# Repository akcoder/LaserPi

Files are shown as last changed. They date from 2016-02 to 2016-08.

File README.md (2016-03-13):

# LaserPi
LaserPi is a Raspberry Pi 2 based auxiliary controller for your laser cutter. Why would you want an auxiliary controller?

LaserPi reads sensor data (temperature, and coolant flow currently) and displays this data on the screen. You can set alarm
information based on the values from the sensors. You can be notified if the temperature goes above a user-defined value, or
if the coolant flow rate goes below a user-defined value. You can also turn on/off your chiller, exhaust, air assist pump,
and lights.

LaserPi can also act upon inputs from your laser controller. Most laser controllers have 4-5 GPIO pins that are set when
the controller is doing certain operations. For example, on the Leetro MPC-6515, output pin 4 is pulled low when the controller
is working. And output pin 1 is pulled low when the air assist box is checked for the layer.

So what can be done with these outputs? LaserPi will automatically turn on your exhaust fan when the laser controller starts
a job, and will keep the exhaust fan running for a user definable period of time after the job is finished to clear away all
the fumes. Have you ever left the air assist box checked by accident and had your air pump turn on when you didn't want it to?
I have, many times and I have to pause my machine and unplug the air assist.

## How does it work?
The brains of the operation is a Raspberry Pi with the code being Python using the QT GUI framework. Data is acquired
from the sensors, and GPIO pins on the Pi, and decisions are made.

###Sensors
*  [Waterproof 1-wire temperature sensors](http://www.aliexpress.com/wholesale?SearchText=waterproof+DS18b20)
*  [YF-S201 fluid flow sensor](http://www.dx.com/p/yf-s201-hall-effect-water-flow-counter-sensor-black-217625)

###Glue components
*  [Logic Level Converter - Bi-Directional](https://www.sparkfun.com/products/12009)
*  [Fotek SSR-25 DA Relays](http://www.amazon.com/dp/B004HZN628)

Here is a work in progress screen shot of LaserPi
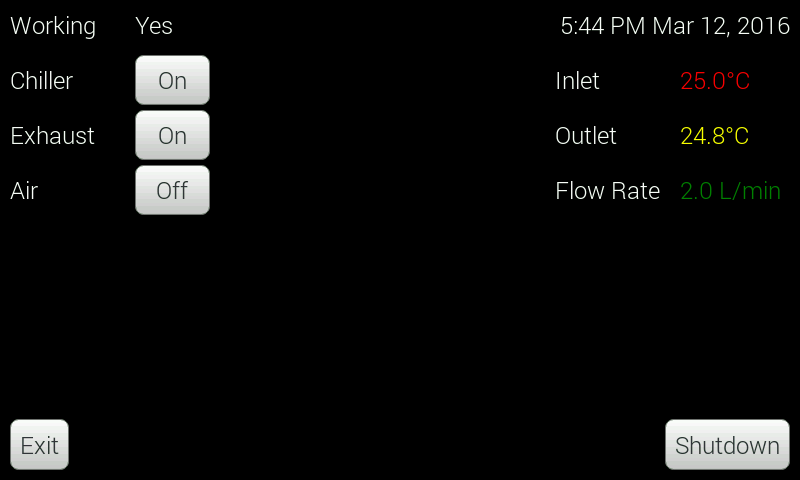
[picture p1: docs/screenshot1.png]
Work in progress


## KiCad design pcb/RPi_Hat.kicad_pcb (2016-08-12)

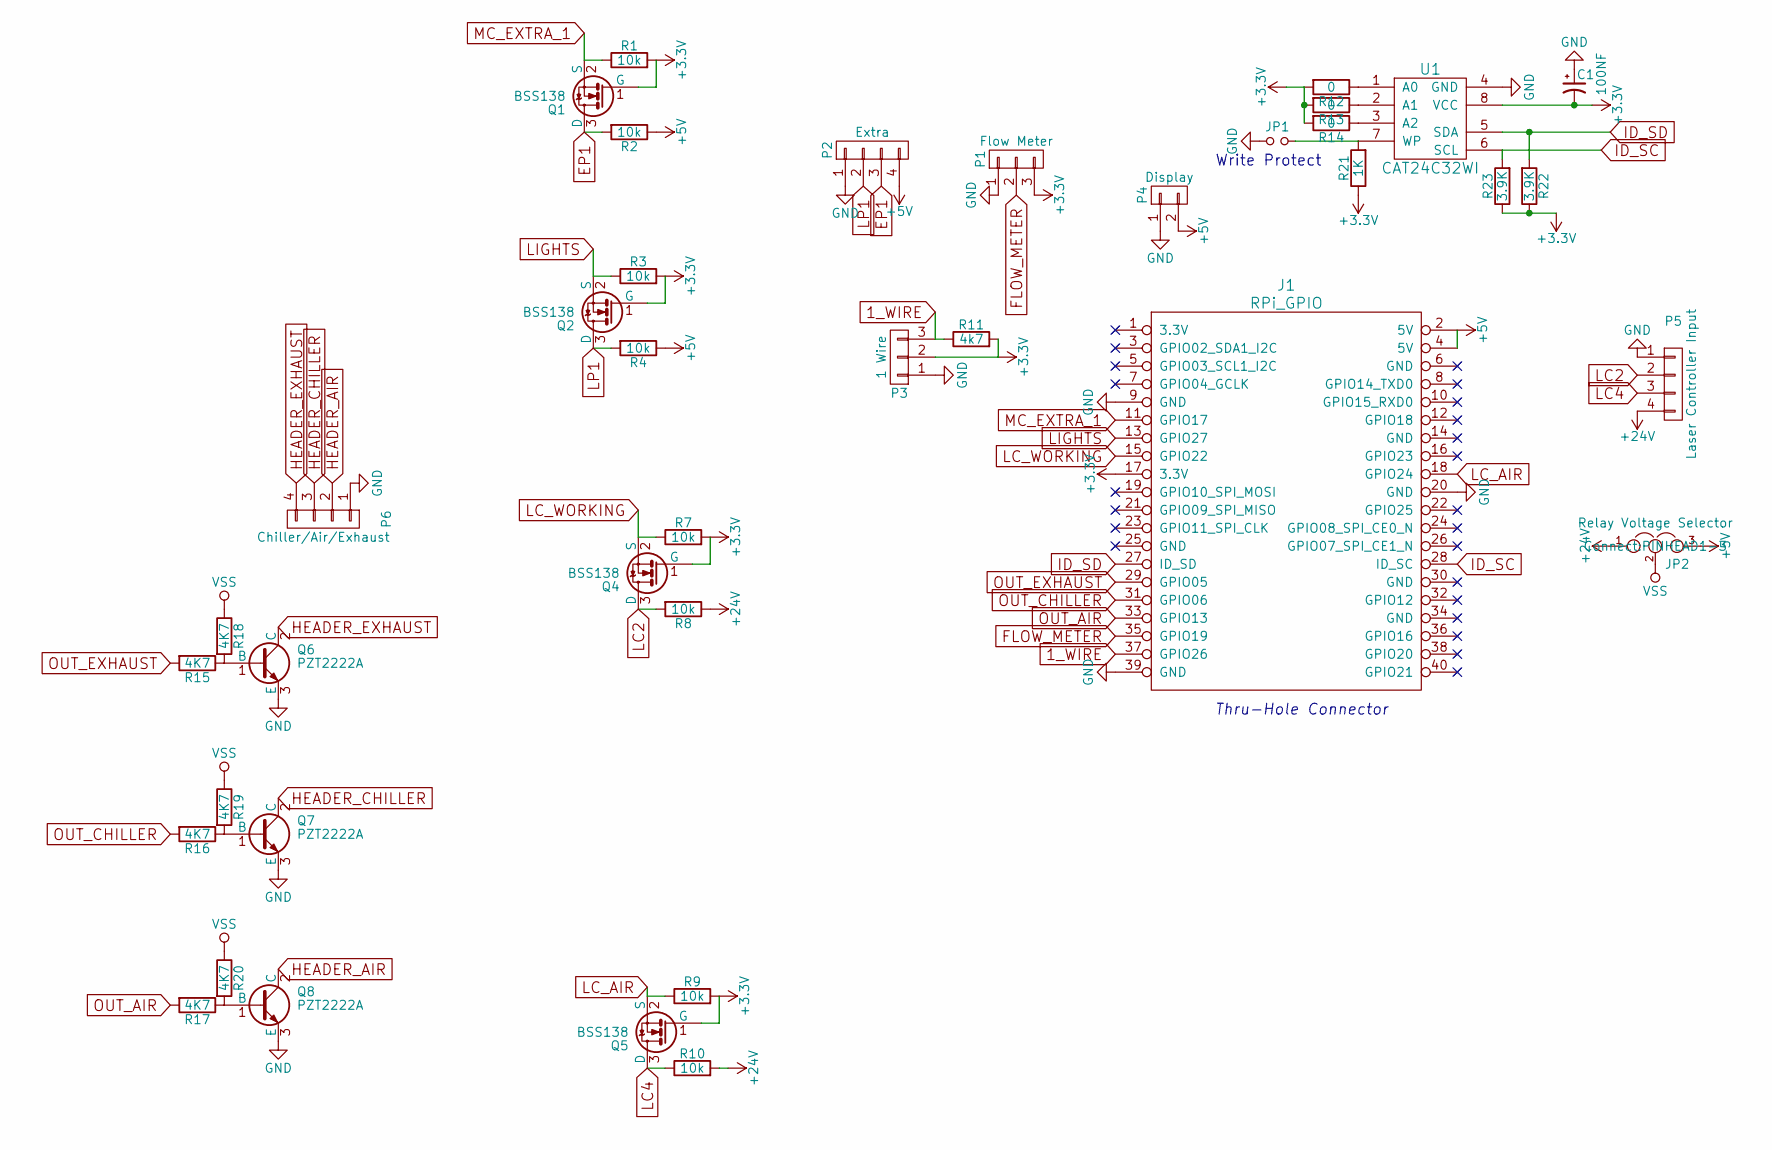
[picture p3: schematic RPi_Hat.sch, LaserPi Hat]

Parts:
C1: 100NF; C_1206_HandSoldering
J1: RPi_GPIO; Pin_Header_Straight_2x20
JP1: Jumper_NO_Small; PINHEAD1-2
JP2: Relay Voltage Selector; PINHEAD1-3
P1: Flow Meter; TerminalBlock_Pheonix_MPT-2.54mm_3pol
P2: Extra; TerminalBlock_Pheonix_MPT-2.54mm_4pol
P3: 1 Wire; TerminalBlock_Pheonix_MPT-2.54mm_3pol
P4: Display; TerminalBlock_Pheonix_MPT-2.54mm_2pol
P5: Laser Controller Input; TerminalBlock_Pheonix_MPT-2.54mm_4pol
P6: Chiller/Air/Exhaust; TerminalBlock_Pheonix_MPT-2.54mm_4pol
Q1, Q2, Q4, Q5: BSS138; SOT-23
Q6, Q7, Q8: PZT2222A; SOT-23
R1, R2, R3, R4, R7, R8, R9, R10: 10k; R_1206_HandSoldering
R11: 4k7; R_1206_HandSoldering
R12, R13, R14: 0; R_0402
R15, R16, R17, R18, R19, R20: 4K7; R_1206_HandSoldering
R21: 1K; R_1206_HandSoldering
R22, R23: 3.9K; R_1206_HandSoldering
U1: CAT24C32WI; SOIC-8-N

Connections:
1_WIRE: J1.37 (GPIO26), P3.3, R11.1
+3V3: C1.2, J1.17 (3.3V), P1.3, P3.2, Q1.1 (G), Q2.1 (G), Q4.1 (G), Q5.1 (G), R1.2, R3.2, R7.2, R9.2, R11.2, R12.2, R13.2, R14.2, R21.1, R22.1, R23.1, U1.8 (VCC)
+5V: J1.2 (5V), J1.4 (5V), JP2.3, P2.4, P4.2, R2.1, R4.1
+24V: JP2.1, P5.4, R8.1, R10.2
EP1: P2.3, Q1.3 (D), R2.2
FLOW_METER: J1.35 (GPIO19), P1.2
GND: C1.1, J1.9 (GND), J1.20 (GND), J1.39 (GND), JP1.1, P1.1, P2.1, P3.1, P4.1, P5.1, P6.1, Q6.3 (E), Q7.3 (E), Q8.3 (E), U1.4 (GND)
HEADER_AIR: P6.2, Q8.2 (C)
HEADER_CHILLER: P6.3, Q7.2 (C)
HEADER_EXHAUST: P6.4, Q6.2 (C)
ID_SC: J1.28 (ID_SC), R23.2, U1.6 (SCL)
ID_SD: J1.27 (ID_SD), R22.2, U1.5 (SDA)
LC2: P5.2, Q4.3 (D), R8.2
LC4: P5.3, Q5.3 (D), R10.1
LC_AIR: J1.18 (GPIO24), Q5.2 (S), R9.1
LC_WORKING: J1.15 (GPIO22), Q4.2 (S), R7.1
LIGHTS: J1.13 (GPIO27), Q2.2 (S), R3.1
LP1: P2.2, Q2.3 (D), R4.2
MC_EXTRA_1: J1.11 (GPIO17), Q1.2 (S), R1.1
unnamed: JP1.2, R21.2, U1.7 (WP)
unnamed: Q6.1 (B), R15.1, R18.2
unnamed: Q7.1 (B), R16.1, R19.2
unnamed: Q8.1 (B), R17.1, R20.2
unnamed: R12.1, U1.1 (A0)
unnamed: R13.1, U1.2 (A1)
unnamed: R14.1, U1.3 (A2)
OUT_AIR: J1.33 (GPIO13), R17.2
OUT_CHILLER: J1.31 (GPIO06), R16.2
OUT_EXHAUST: J1.29 (GPIO05), R15.2
VSS: JP2.2, R18.1, R19.1, R20.1

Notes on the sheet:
Thru-Hole Connector
Write Protect

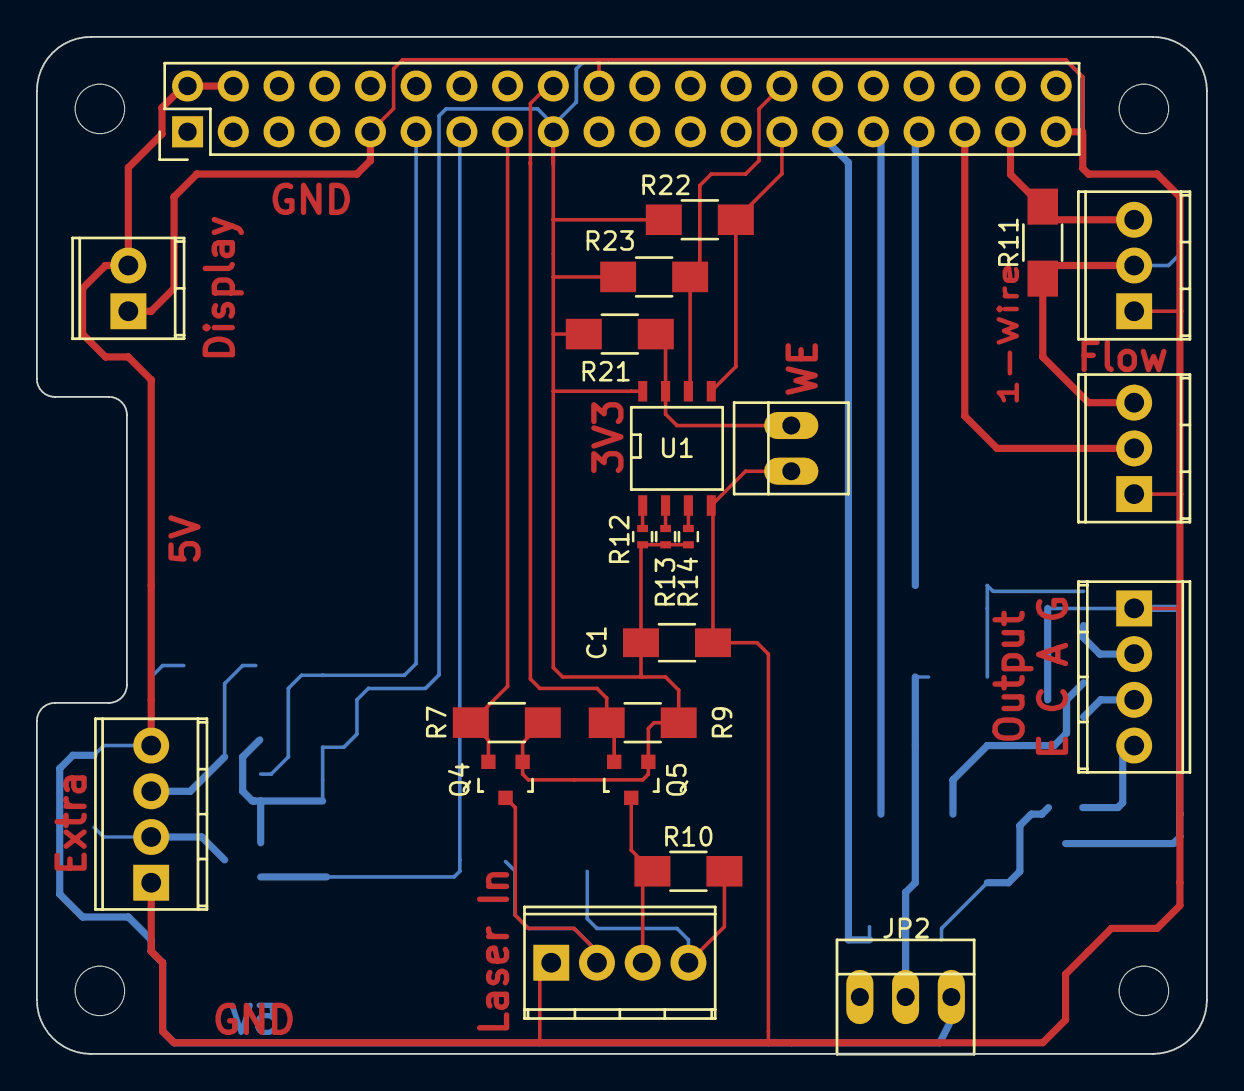
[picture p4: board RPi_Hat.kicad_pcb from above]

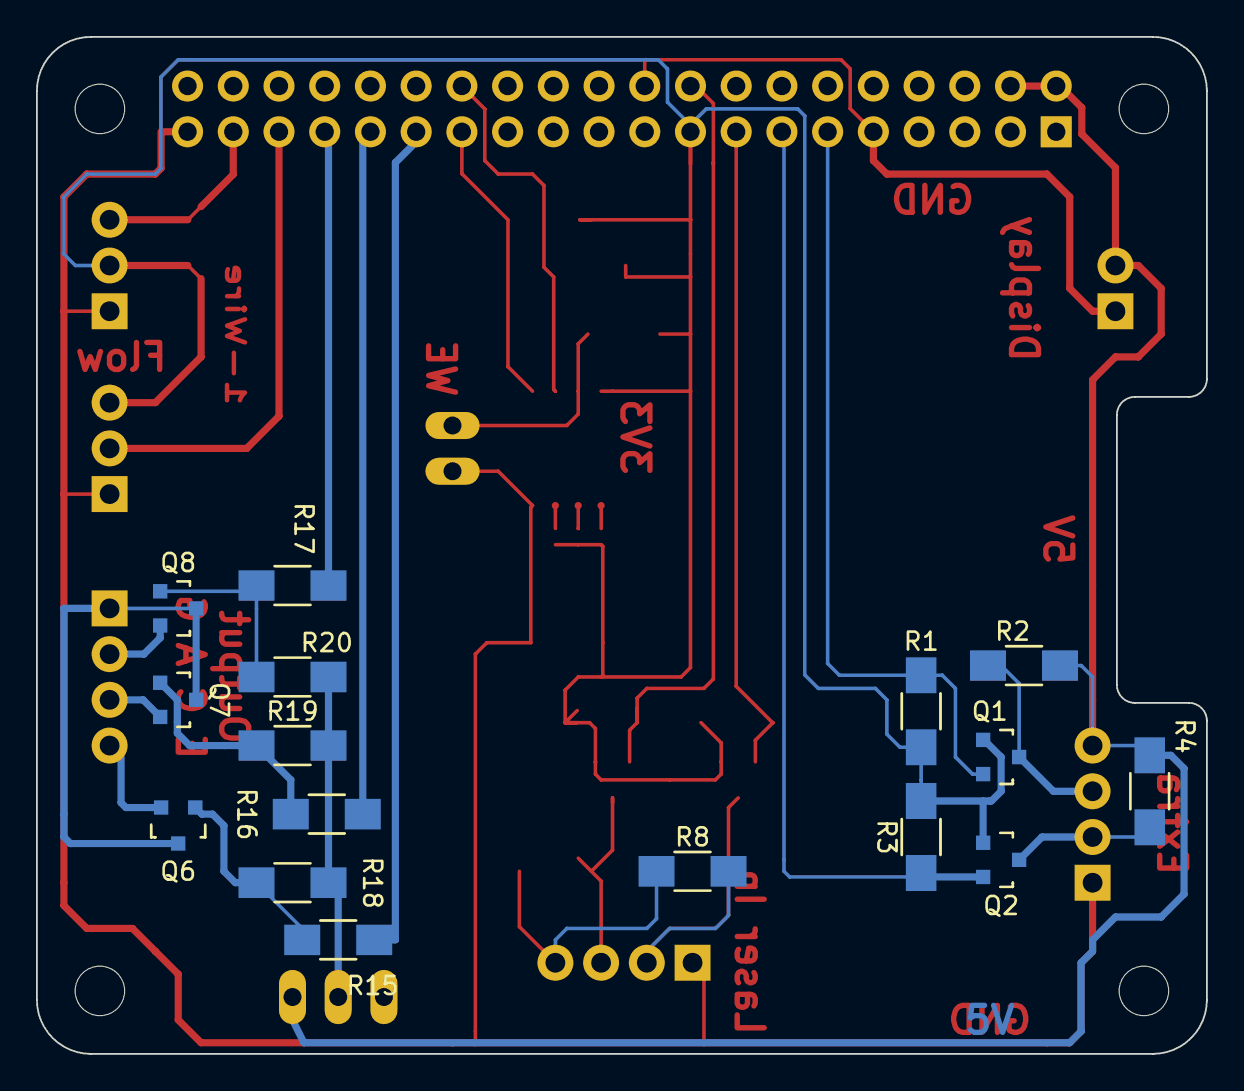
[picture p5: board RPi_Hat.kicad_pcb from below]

Board: 2 copper layers, 65.0 x 56.5 mm, 39 parts (16 on the bottom side), 30 nets.

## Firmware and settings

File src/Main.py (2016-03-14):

"""Main"""
import logging
import sys
import signal
#import ptvsd
#ptvsd.enable_attach('laserpi')

from PySide.QtGui import QApplication

from ViewModel import MainViewModel
from Views import MainView
from Controller import Controller
from Helpers.Settings import Settings

def setup_logging():
    logger = logging.getLogger('')
    logger.setLevel(logging.DEBUG)
    ch = logging.StreamHandler()
    ch.setLevel(logging.DEBUG)
    # create formatter and add it to the handlers
    formatter = logging.Formatter('%(asctime)s - %(name)s - %(levelname)s - %(message)s')
    ch.setFormatter(formatter)
    logger.addHandler(ch)

def main():
    """Main"""
    signal.signal(signal.SIGINT, signal.SIG_DFL)

    setup_logging()

    # Create Qt application and the QDeclarative view
    app = QApplication(sys.argv)

    view_model = MainViewModel()
    controller = Controller(view_model)

    main_view = MainView(view_model)

    if sys.platform == 'win32':
        main_view.show()
    else:
        main_view.showFullScreen()

    sys.exit(app.exec_())

if __name__ == "__main__":
    main()

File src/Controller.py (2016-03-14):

"""The glue between the view and viewModel"""

import os
import logging
import sys
import threading
from threading import Thread, Timer
from PySide import QtCore
from ViewModel import MainViewModel
from Helpers import Settings
from enum import IntEnum
from Helpers.PerpetualTimer import PerpetualTimer
from Helpers.Observer import Observer
from Sensors.SensorFactory import SensorFactory

if sys.platform == 'linux':
    import RPi.GPIO as GPIO

class Controller(Observer):
    """The glue between the view and viewModel"""

    __logger = logging.getLogger(__name__)
    def __init__(self, viewModel: MainViewModel):
        Observer.__init__(self)
        self.__view_model = viewModel
        self.__gpio_is_setup = False
        self.__exhaust_timer = None
        self.__view_model.onChillerChanged.connect(self.chiller_changed)
        self.__view_model.onAirChanged.connect(self.air_changed)
        self.__view_model.onExhaustChanged.connect(self.exhaust_changed)
        self.__view_model.onExitClicked.connect(self.close)
        self.__view_model.onShutdownClicked.connect(self.shutdown)
        self.__sensors = []

        if sys.platform == 'linux':
            self._states = {
                Settings.instance.pins.input.working:GPIO.LOW,
                Settings.instance.pins.input.airTrigger:GPIO.LOW
            }

            self.__gpio_thread = Thread(target=self.__setup_gpio)
            self.__gpio_thread.setDaemon(1)
            self.__gpio_thread.start()

        self.observe('temp_changed', self.handle_temp_changed)
        self.observe('flow_changed', self.handle_flow_changed)

        for key in Settings.instance.sensors._fields:
            config = getattr(Settings.instance.sensors, key)
            sensor = SensorFactory.factory(key, config)
            sensor.start();
            self.__sensors.append(sensor)

    def __del__(self):
        self.__logger.info('Destructor called, cleaning up')
        self.cleanup()

    def __setup_gpio(self) -> None:
        self.__logger.info("Setting up GPIO")
        GPIO.setmode(GPIO.BCM)

        for key in Settings.instance.pins.output._fields:
            pin = getattr(Settings.instance.pins.output, key)
            self.__logger.debug("Setting GPIO {0} for output".format(pin))
            GPIO.setup(pin, GPIO.OUT)

        GPIO.setup(Settings.instance.pins.input.working, GPIO.IN, pull_up_down=GPIO.PUD_DOWN)
        GPIO.add_event_detect(Settings.instance.pins.input.working, GPIO.BOTH, callback=self.working_changed, bouncetime=25)

        GPIO.setup(Settings.instance.pins.input.airTrigger, GPIO.IN, pull_up_down=GPIO.PUD_DOWN)
        GPIO.add_event_detect(Settings.instance.pins.input.airTrigger, GPIO.BOTH, callback=self.air_trigger_changed, bouncetime=25)

        self.__gpio_is_setup = True

    def close(self):
        self.__logger.info("Close called")
        self.cleanup()
        self.__logger.info("After cleanup")
        QtCore.QCoreApplication.instance().quit()

        self.__logger.info("OS exit")
        os._exit(0)
        raise SystemExit

    @classmethod
    def shutdown(cls):
        if sys.platform == "linux":
            try:
                command = "/usr/bin/sudo /sbin/shutdown --halt now"
                import subprocess
                process = subprocess.Popen(command.split(), stdout=subprocess.PIPE)
                output = process.communicate()[0]
                self.__logger.info(output)
            except Exception as ex:
                self.__logger.error(ex)
                self.__logger.error("Unable to shutdown")
                sys.exit()
        else:
            sys.exit()

    def cleanup(self):
        self.__logger.info("Cleanup called")

        for sensor in self.__sensors:
            sensor.stop()

        if sys.platform == 'linux' and self.__gpio_is_setup:
            self.__logger.info("Cleaning up GPIO")
            GPIO.cleanup()

    def handle_temp_changed(self, name: str, value: float) -> None:
        self.__view_model.onTemperatureChanged.emit(name, value)

    def handle_flow_changed(self, name: str, value: float) -> None:
        self.__view_model.onFlowRateChanged.emit(name, value)

    def air_changed(self) -> None:
        if sys.platform != 'linux':
            return

        self.set_air_state(GPIO.HIGH if self.__view_model.air else GPIO.LOW)

    @QtCore.Slot()
    def air_trigger_changed(self, channel=None):
        if  GPIO.input(channel) == GPIO.HIGH:
            if  self._states[channel] == GPIO.LOW:
                self.__logger.debug("Turning air on because triggered")
                self.__view_model.air = True

            self._states[channel] = GPIO.HIGH
        elif self._states[channel] == GPIO.HIGH and self.__view_model.air:
            self.__logger.debug("Turning air off because triggered")
            self.__view_model.air = False
            self._states[channel] = GPIO.LOW

    def set_air_state(self, state):
        self.set_pin_state(Settings.instance.pins.output.airOutput, state)

    def set_pin_state(self, pin: int, state: bool) -> None:
        self.__logger.debug("Setting GPIO {0} to {1}".format(pin, "HIGH" if state else "LOW"))
        GPIO.output(pin, GPIO.HIGH if state else GPIO.LOW)

    def working_changed(self, channel):
        if  GPIO.input(channel) == GPIO.HIGH:
            if  self._states[channel] == GPIO.LOW:
                self.__logger.info("Laser is working")
                self.__view_model.working = True
                self.turn_exhaust_on()

                if self.__exhaust_timer is not None:
                    self.__exhaust_timer.cancel()
                    self.__exhaust_timer = None

            self._states[channel] = GPIO.HIGH
        elif self._states[channel] == GPIO.HIGH:
            if self.__view_model.exhaust:
                assert self.__exhaust_timer is None, "Exhaust timer should have been set to null!"

                seconds = Settings.instance.exhaust_time_after_finished
                self.__logger.info("Setting exhaust off timer for %d seconds" % seconds)
                self.__exhaust_timer = Timer(seconds, self.turn_exhaust_off)
                self.__exhaust_timer.start()
                self.__view_model.working = False
            self._states[channel] = GPIO.LOW

    def turn_exhaust_on(self):
        self.__logger.debug("Turning exhaust fan on")
        self.__view_model.exhaust = True
        self.set_pin_state(Settings.instance.pins.output.exhaust, GPIO.HIGH)

    def turn_exhaust_off(self):
        self.__logger.debug("Turning exhaust fan off")
        self.__view_model.exhaust = False
        self.__exhaust_timer = None
        self.set_pin_state(Settings.instance.pins.output.exhaust, GPIO.LOW)

    @QtCore.Slot()
    def chiller_changed(self):
        if sys.platform == 'linux':
            self.set_pin_state(Settings.instance.pins.output.chiller, self.__view_model.chiller)
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

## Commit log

2016-02-29 - Add exit button - Make exiting the app cleanup the GPIO - Misc pylint cleanups - Trigger more GPIOs - Figure out the final pin configuration
2016-03-05 Add Temperature and FlowMeter support Add settings support
2016-03-06 Rename LaserPi -> LaserPiPy
2016-03-06 LaserPiIot initial commit
2016-03-06 Add the LaserPiPy project files
2016-03-10 Dynamically load the temperature sensors from the config and add them to the display Do a fade in animation when the temp is first set in the view
2016-03-11 Setup flow rate sensor
    Setup the flow rate sensor
    Don't use a property on the view model to hold the degree symbol, put it
    in the Temperature.js file
2016-03-11 Show units for temperature
    Don't do all the rejiggering of the config json to and from an object to
    put it into the QML.
2016-03-12 Fix layout issues, temp changes
    Fix some layout nits
    Put the degree symbol and temp units in their own label and right align
    the temperature
    [Temperature.py]
2016-03-12 Use factory to create sensors
    Use the factory pattern to create the sensors, and pass the config into
    the sensors.
2016-03-12 Globals are bad!
    Get rid of all the globals in Temperature.js by using lambdas!
2016-03-12 Cleanup temperature view
    Make the temperature view more generic
    Remove the model from the temperature view and set properties on the
    view
2016-03-12 More cleanup
    Move the units into the sensor item. This allows you to have different
    units on a per sensor basis.
    Wire up the flow meter sensor
2016-03-13 Add threshold colors to the flow meter
2016-03-14 Switch from print to logging
2016-04-03 Switch the 1 wire GPIO
    From the default of pin 4 to 26. This works out better for the pcb
2016-04-03 Pi HAT
    Pi HAT schematic and PCB done in KiCAD
    [RPi_GPIO.sch, RPi_Hat.kicad_pcb, RPi_Hat.sch]
2016-04-04 Make PCB layout cleaner
    Swap some things around to make the layout cleaner
2016-04-05 Schematic updates
    Don't use a relay, use a level shifter so the pin can be used as either
    an input or an output.
    [RPi_GPIO.sch, RPi_Hat.kicad_pcb, RPi_Hat.sch]
2016-04-14 Add outputs
    for the chiller, exhaust, air
    [RPi_Hat.kicad_pcb, RPi_Hat.sch]
2016-04-15 Add passives for the EEPROM
    [RPi_Hat.kicad_pcb, RPi_Hat.sch]
2016-04-16 Update the schematic and board files
2016-04-19 Add labels to pcb
    [RPi_Hat.kicad_pcb]
2016-05-05 Adjust flow-meter correction factor
2016-08-12 Update the schematic
    [RPi_Hat.kicad_pcb, RPi_Hat.sch, _saved_RPi_Hat.sch]
